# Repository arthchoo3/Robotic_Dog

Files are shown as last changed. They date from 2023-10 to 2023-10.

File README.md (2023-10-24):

# Robotic_Dog
This repository displays my robotic dog project, including the STL, Gerber, and Ino files. It also offers a glimpse into my thoughts and ideas throughout the design process, including previous iterations of various design aspects.

## General Overview
 The dog is made of 143 3D-printed pieces, 5 custom PCBs, and 12 servo motors. Each leg of the dog is 30cm long and contains three MG996R servo motors: two for shoulder actuation on two axes and one for knee actuation. Each leg has one PCB that distributes power and signal to the three servos. The central PCB is controlled by an ATMega328 microcontroller and distributes power and signal to each of the four leg PCBs. The code is written in Arduino C++.


Dog Parts
Dog 2 Leg

https://github.com/arthchoo3/Robotic_Dog/assets/140445967/36175da8-d79e-43d7-8e23-6a641d8918cc

## Joint Design
In my first attempt at building a robotic dog, I attempted to mount the structural components of the legs directly to the servo horns. This design did not work because the servo horns were not designed to withstand forces perpendicular to their plane of rotation. So, for this dog, I went for a design approach in which the bending forces act not on the servo horn itself but on a rotary guide and hub system. This makes it so the servos must only resist the torsion forces for which they were designed.

The servo motor (blue) rotates the cylinder (green) which rotates the leg strut (gray) and the hub (yellow). Any bending forces that the leg strut would have previously placed on the servo horn are now supported by the rotary guide (red), making the servo only responsible for rotating the system.
Dog 2 Joint

## PCBs
For the microcontroller, I chose to use the ATMega328 from an Arduino Uno because I am very familiar with C++ and the Arduino IDE. The central PCB has four sets of three-prong plugs, one plug for each leg and one prong for each servo. It also has four sets of positive and negative outputs to power each leg. Each leg also has its own PCB into which the three servos plug to connect to the central PCB.
The PCBs are also decorated with symbols of the vibrant programming community at my school.  
Dog Main PCB
Dog knee PCB

## Code and Calculations
The code is written in Arduino C++ and uses the following math to calculate servo angles based on X (horizontal distance from shoulder) and Z (vertical distance from shoulder) coordinates of the foot. This system allows for smooth linear motion and easier programming.
Dog Math

## Setbacks and Limitations
The MG996R Servos that the dog currently uses do not have enough torque to properly carry the dog's weight. This is why the dog leans forward as it walks because if the weight isn’t shifted more to the front legs, the rear motors will give out under the dog's weight. This is also the reason the dog must be plugged into a power supply because the servos cannot support the weight of a battery pack. I am currently saving money from my weekend job to buy higher torque servos so this won’t be an issue in the future. 

## Future Plans
Right now, the very basic PCB that controls the dog only allows for pre-programmed motion. I am currently learning to work with CH340C USB to Serial converters so I can add USB ports to make the dog remote-controlled. I also plan to buy higher torque servos once I have saved enough money so the dog can move more fluidly.

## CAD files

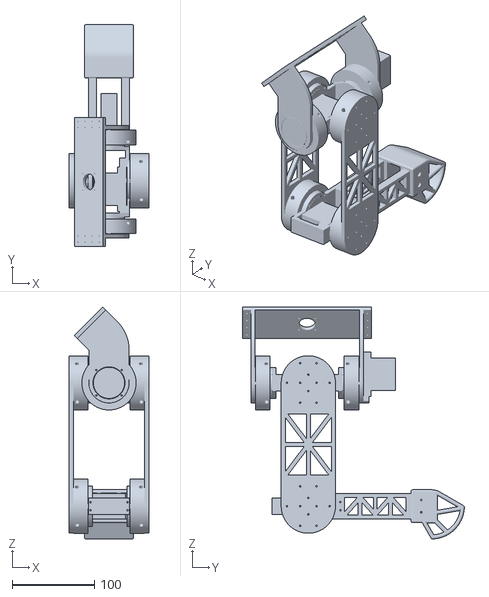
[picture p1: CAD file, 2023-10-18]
Dog Full leg.stl
97.0 x 270.0 x 282.3

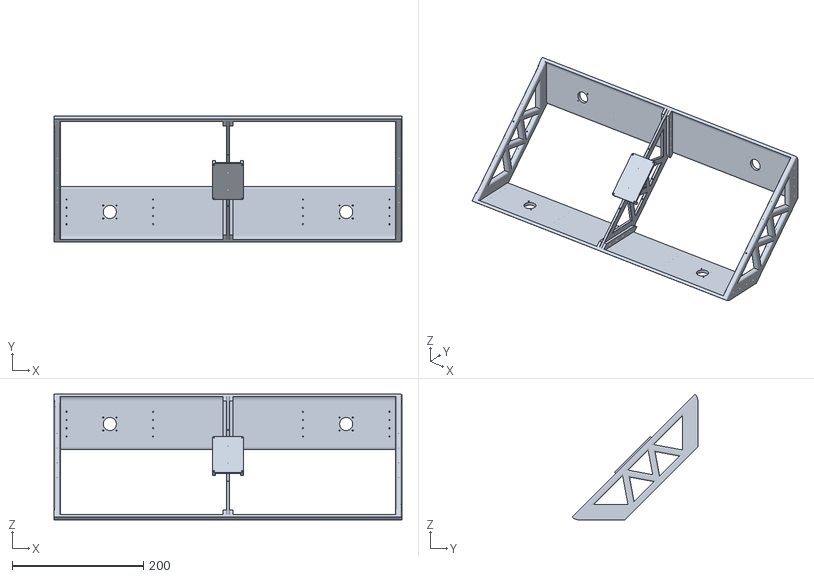
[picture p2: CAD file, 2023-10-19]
Dog Body.stl
530.0 x 191.7 x 191.7

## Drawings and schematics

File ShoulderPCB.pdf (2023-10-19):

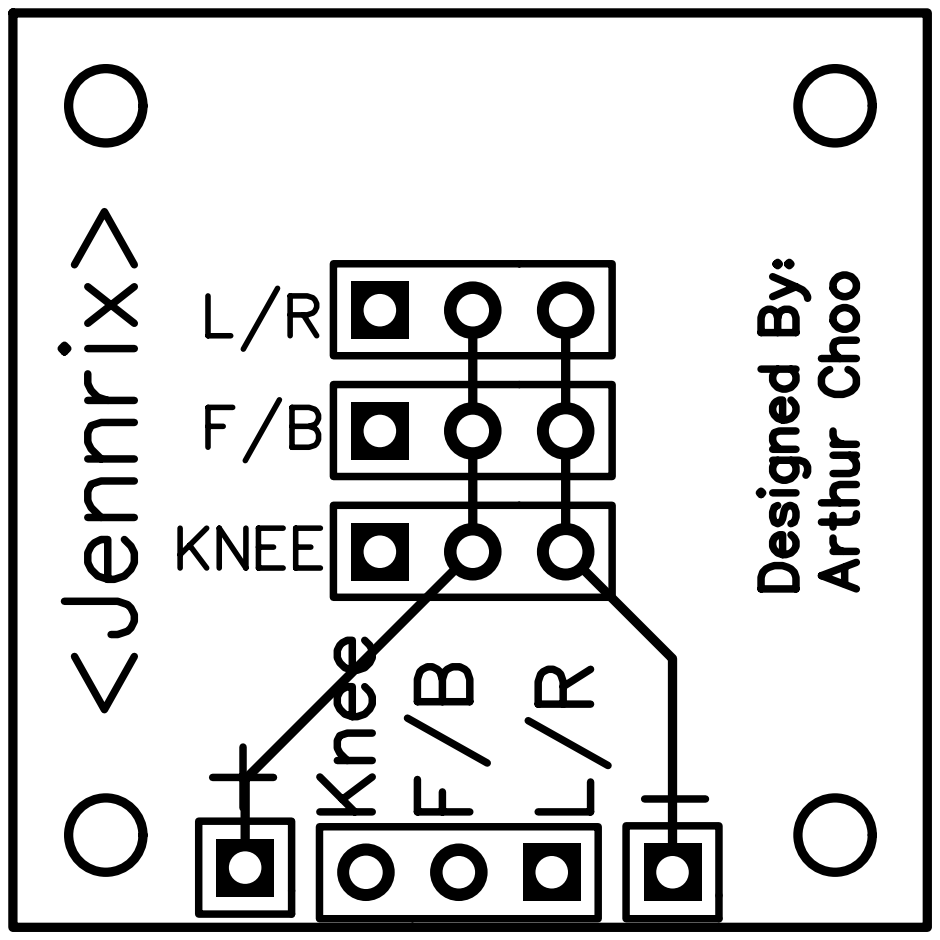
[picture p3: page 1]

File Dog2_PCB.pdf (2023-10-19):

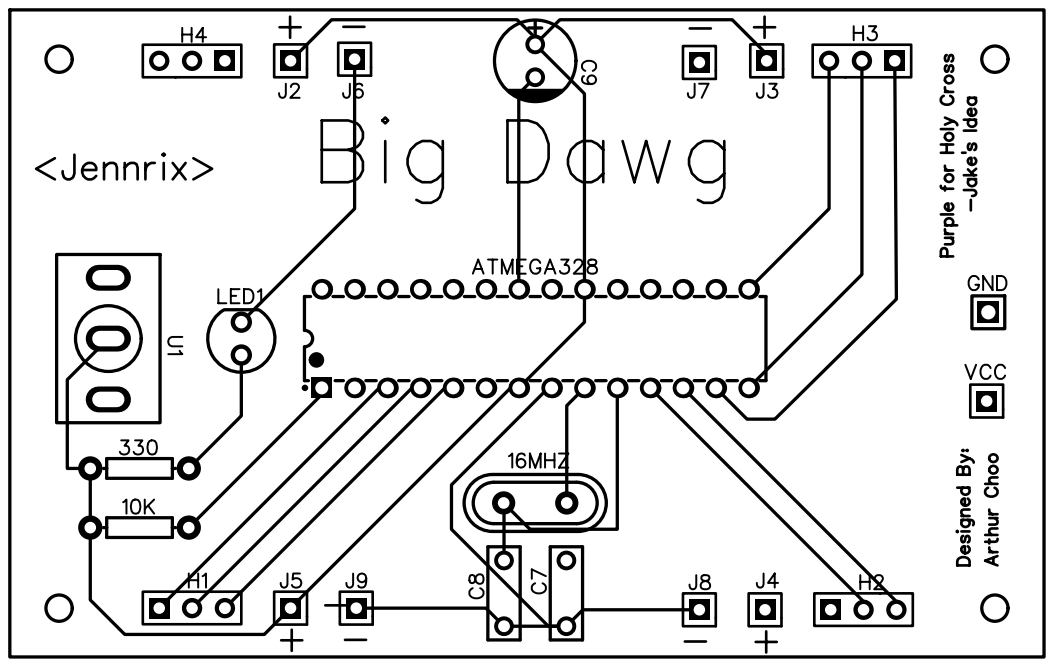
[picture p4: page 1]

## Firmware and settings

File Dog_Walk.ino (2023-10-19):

#include<Servo.h>

float leg_length = 15;

int del = 3;
float stepSize = 0.05;

Servo servo[4][3];
//    servo[leg#][servo number]
//               [knee = 0, F_B = 1, L_R = 2]

//Index of motors in array
int knee = 0, F_B = 1, L_R = 2;

//Index of legs in array
int BL = 0, BR = 1, FR = 2, FL = 3;

//max/min x/z values when walking
float xMin = -10.0, xMax = -2.0, zMin = 16.0, zMax = 20.0;

float pos[4][2];
//             [leg#][x, z]

//Index of X and Z coordinates in array
int xPos = 0,  zPos = 1;


//###################################### Set Up ######################################
void setup() 
{
 
  //=========================================
  //Assigns pins to servos
  //Sets leg positions to squat position
  int pin = 1;
  for(int leg = 0; leg < 4; leg++)
  {
    pos[leg][xPos] = xMax;
    pos[leg][zPos] = zMin;
    for(int motor = 0; motor < 3; motor++)
      {
        servo[leg][motor].attach(pin);
        pin++;
      }
  }
   //========================================


   //========================================
   //Moves legs to squat position
    for(int legNum = 0; legNum < 4; legNum++)
      update_leg(legNum);
   //========================================


  //=========================================
  //Stand Up
  for(float z = zMin; z <= zMax; z += stepSize)
    for (int leg = 0; leg < 4; leg++)
     {
       pos[leg][zPos] = z;
       update_leg(leg); 
       delay(del);
     }
   //=========================================

   delay(5000);
}
//####################################################################################



//*****************************Angle Calculations**************************************
//Calculates Shoulder servo angle based on foot x and z coordinates
float shoulder_ang(float x, float z)
{return 90 + to_degrees(atan(abs(x)/z)) * (x>0?1:-1) - ((180 - knee_ang(x,z))/2);}

//Calculates Knee servo angle based on foot x and z coordinates
float knee_ang(float dist, float z)
{return to_degrees(acos(1 - ((dist*dist + z*z)/(2*leg_length*leg_length))));}

//Converts radians to degrees
float to_degrees(float rads)
{return (180 * rads / PI);}
//*************************************************************************************

void loop() 
{
  walk_forward();
}

void leg_step_forward(int legNum)
{
  int ZMin, ZMax;
  //lift leg up
  if(legNum < 2) //Rear Legs extend more for balance --> servos aren't strong enough to balance otherwise
  {
    ZMin = 19;
    ZMax = 22;
  }
  else
  {
    ZMin = 16;
    ZMax = 19;
  }
  while (pos[legNum][zPos] >= ZMin)
    {
      pos[legNum][zPos]-=stepSize;
      update_leg(legNum);
      delay(del);
    }
  //move leg forward
  while (pos[legNum][xPos] <= xMax)
    {
      pos[legNum][xPos]+=stepSize;
      update_leg(legNum);
      delay(del);
    }
  //move leg back down
  while (pos[legNum][zPos] <= ZMax)
    {
      pos[legNum][zPos]+=stepSize;
      update_leg(legNum);
      delay(del);
    }
}

void walk_forward()
{  
  while (!reachedMin())
  {
    for(int legNum = 0; legNum < 4; legNum++)
    {
      pos[legNum][xPos] -= stepSize;
      update_leg(legNum);
    }
    delay(del);
  }
  delay(1000);
  
  leg_step_forward(BL);
  delay(50);
  leg_step_forward(BR);
  delay(50);
  leg_step_forward(FL);
  delay(50);
  leg_step_forward(FR);
}

bool reachedMin()
{
  return (pos[BL][xPos] <= xMin && pos[BR][xPos] <= xMin && pos[FR][xPos] <= xMin && pos[FL][xPos] <= xMin);
}

//************************Updagtes Leg Based on coordinates in pos[][]*******************
void update_leg(int legNum)
{
    servo[legNum][F_B].write(shoulder_ang(pos[legNum][xPos], pos[legNum][zPos]));
    servo[legNum][knee].write(knee_ang(pos[legNum][xPos], pos[legNum][zPos]));
}
//****************************************************************************************
